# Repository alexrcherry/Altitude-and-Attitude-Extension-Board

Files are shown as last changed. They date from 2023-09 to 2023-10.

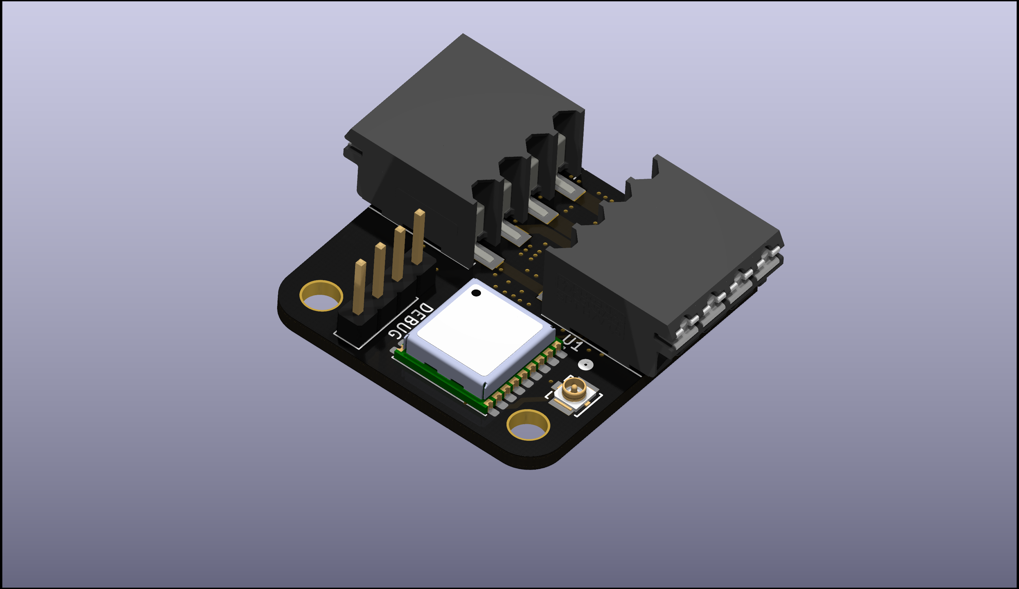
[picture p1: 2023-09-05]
AT&T/ATL_BACK.png

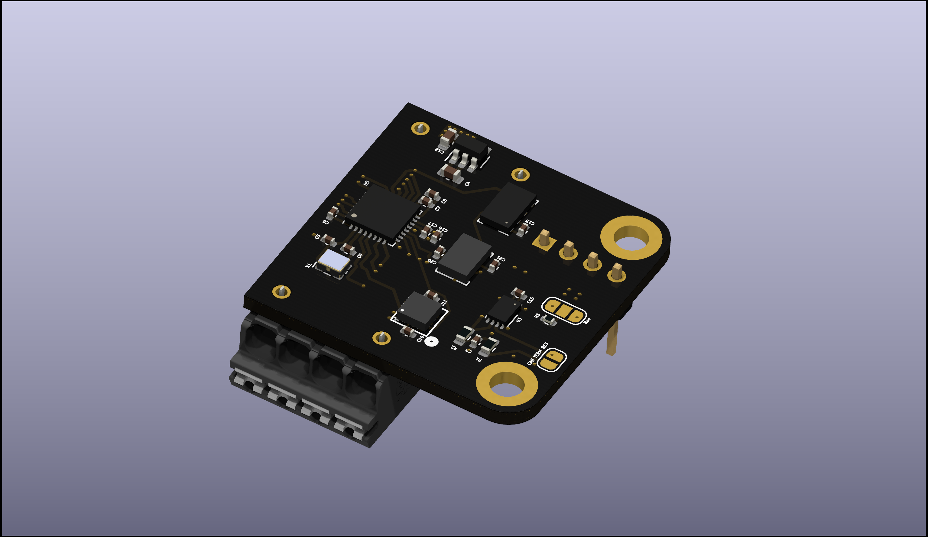
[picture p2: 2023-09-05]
AT&T/ATL_FRONT.png

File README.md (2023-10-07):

# Altitude-and-Attitude-Extension-Board
PCB design files for altitude and attitude extension board
## Purpose
The purpose of the Altitude and Attitude Extension Board is to measure the full state of a rocket. To do this, a gyroscope, accelerometer, gps, barometer and magnetometer are included on this board. A Kalman filter or some other means is necessary to get the full state of the rocket from the sensor data. The full state output of this board will be used to estimate the apogee of the rocket and to provide feedback for control systems.

| Requirement # | Requirement | Justification | Testing Plan |
| --- | --- | --- | --- |
| R-001 | Shall fit in 4” diameter body tube | PCB needs to fit into L1 kits & Olympus expected diameter. | Measure with calipers |
| R-002 | Will use 2x M2 or larger mounting bolts | Needs to be mounted easily inside the avionics bay. | X |
| R-003 | Will use 5v input power supply | The main power bus running the length of the rocket is 5v. | X |
| R-004 | Will draw less than 1A | The device should not greatly affect the power bus for other devices. Current is limited so that voltage sag is minimized. | X |
| R-005 | Will have 2x CAN high connection | Needs two connections so the device can be daisy chained. | X |
| R-006 | Will have 2x CAN low connections  | Needs two connections so the device can be daisy chained. | X |
| R-007 | Will have 2x Gnd connections | Needs two connections so the device can be daisy chained. | X |
| R-008 | Will have 2x 5v+ connections | Needs two connections so the device can be daisy chained. | X |
| R-009 | Will fulfill the requirements across the temperature range of -90 to 50 deg C | Needs to work in the sun on the launch pad and in the cold upper atmosphere. | Real conditions, freezer, oven? |
| R-010 | Will use CAN 2.0 | Communication needs to be compatible with all other boards, can 2.0 chosen for high speed. | X |
| R-011 | Should use STM32 microcontroller | This requirement is somewhat flexible, stm32 is greatly preferred because that is what the club currently has experience with. | X |
| R-012 | Should have greater than 1 deg heading accuracy over flight time | This information may be used for active control and needs to be as accurate as possible to minimize rocket dispersion. | |
| R-013 | Should be able to measure 10 g or greater acceleration | Testing will be done on solid rockets which generally have greater acceleration. | |
| R-014 | Should be able to measure altitude within < 5% error to 130km | Needs to measure altitude for a spaceshot. This may end up being done with radio ranging instead of IMU integration. | |
| R-015 | Should be able to detect launch, apogee, and landing | Software needs to send a signal to the main processing board for these important flight events so that logging rate can be modified. | |

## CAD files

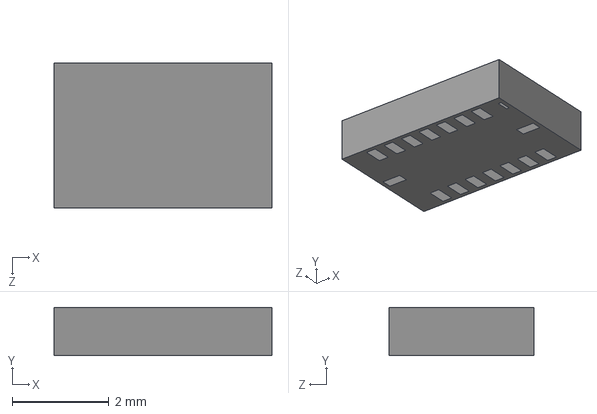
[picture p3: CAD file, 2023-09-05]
AT&T/Imported Symbols and Footprints/BMI088/KiCADv6/BMI088--3DModel-STEP-56544.STEP
4.50 x 1.00 x 3.00 mm

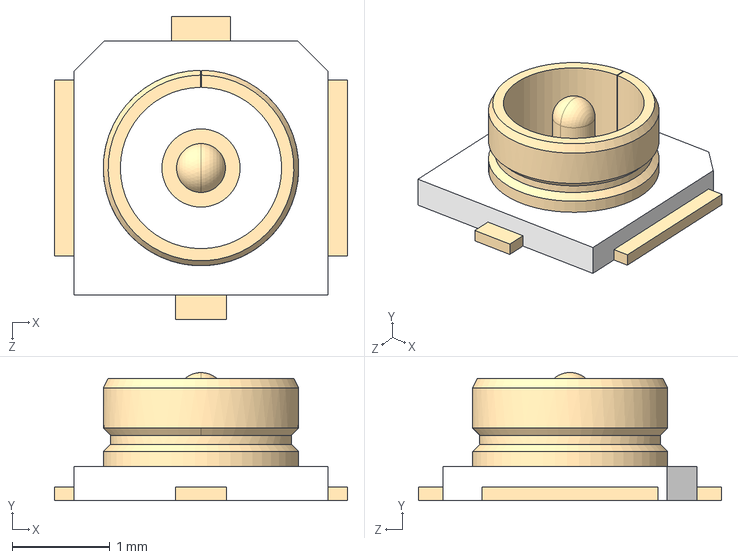
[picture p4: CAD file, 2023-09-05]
AT&T/Imported Symbols and Footprints/CONMHF1-SMD-G-T/CONMHF1-SMD-G-T.step
3.00 x 1.31 x 3.10 mm

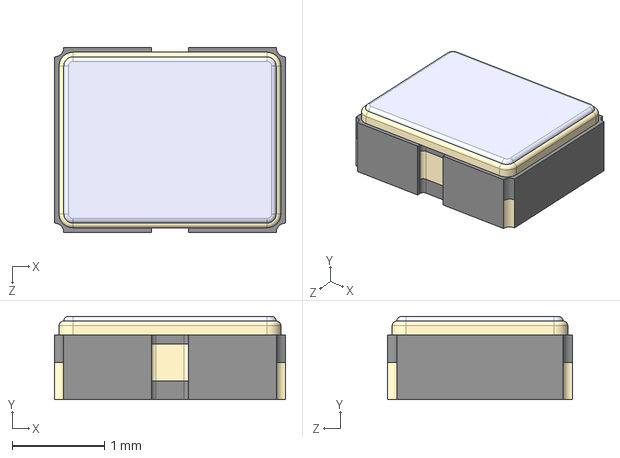
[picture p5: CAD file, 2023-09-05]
AT&T/Imported Symbols and Footprints/ECS-2520/ECS-2520MV-120-BN-TR.STEP
2.50 x 0.9 x 2.00 mm

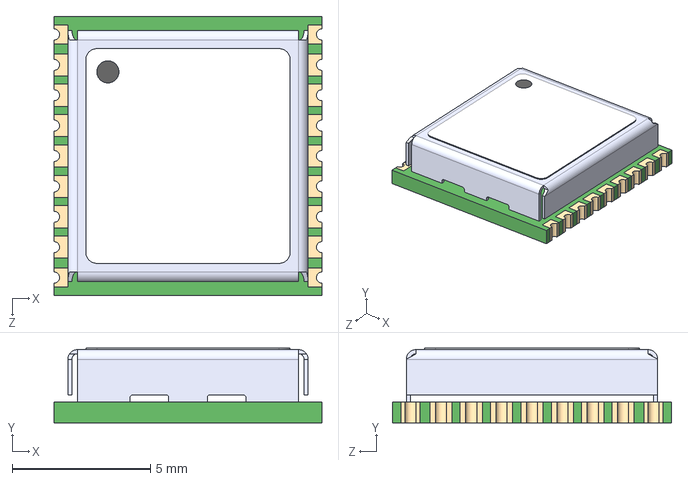
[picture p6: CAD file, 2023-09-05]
AT&T/Imported Symbols and Footprints/MAX-M10S/MAX-M8C-0-10--3DModel-STEP-56544.STEP
9.70 x 2.70 x 10.1 mm

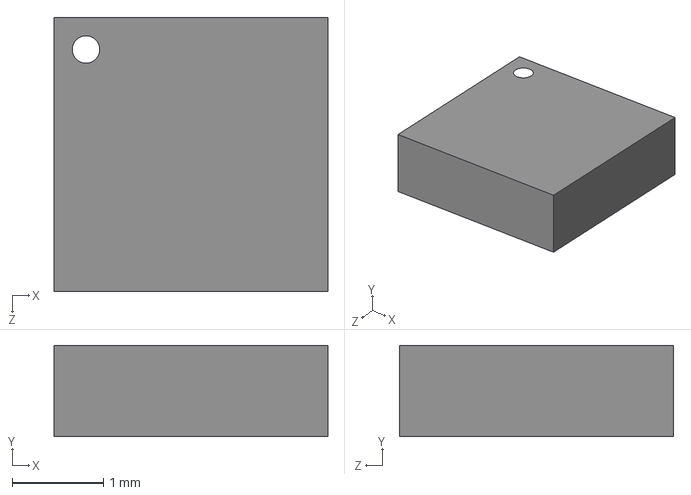
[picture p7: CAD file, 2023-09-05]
AT&T/Imported Symbols and Footprints/MMC5983MA/KiCADv6/MMC5983MA--3DModel-STEP-269445.STEP
3.00 x 1.00 x 3.00 mm

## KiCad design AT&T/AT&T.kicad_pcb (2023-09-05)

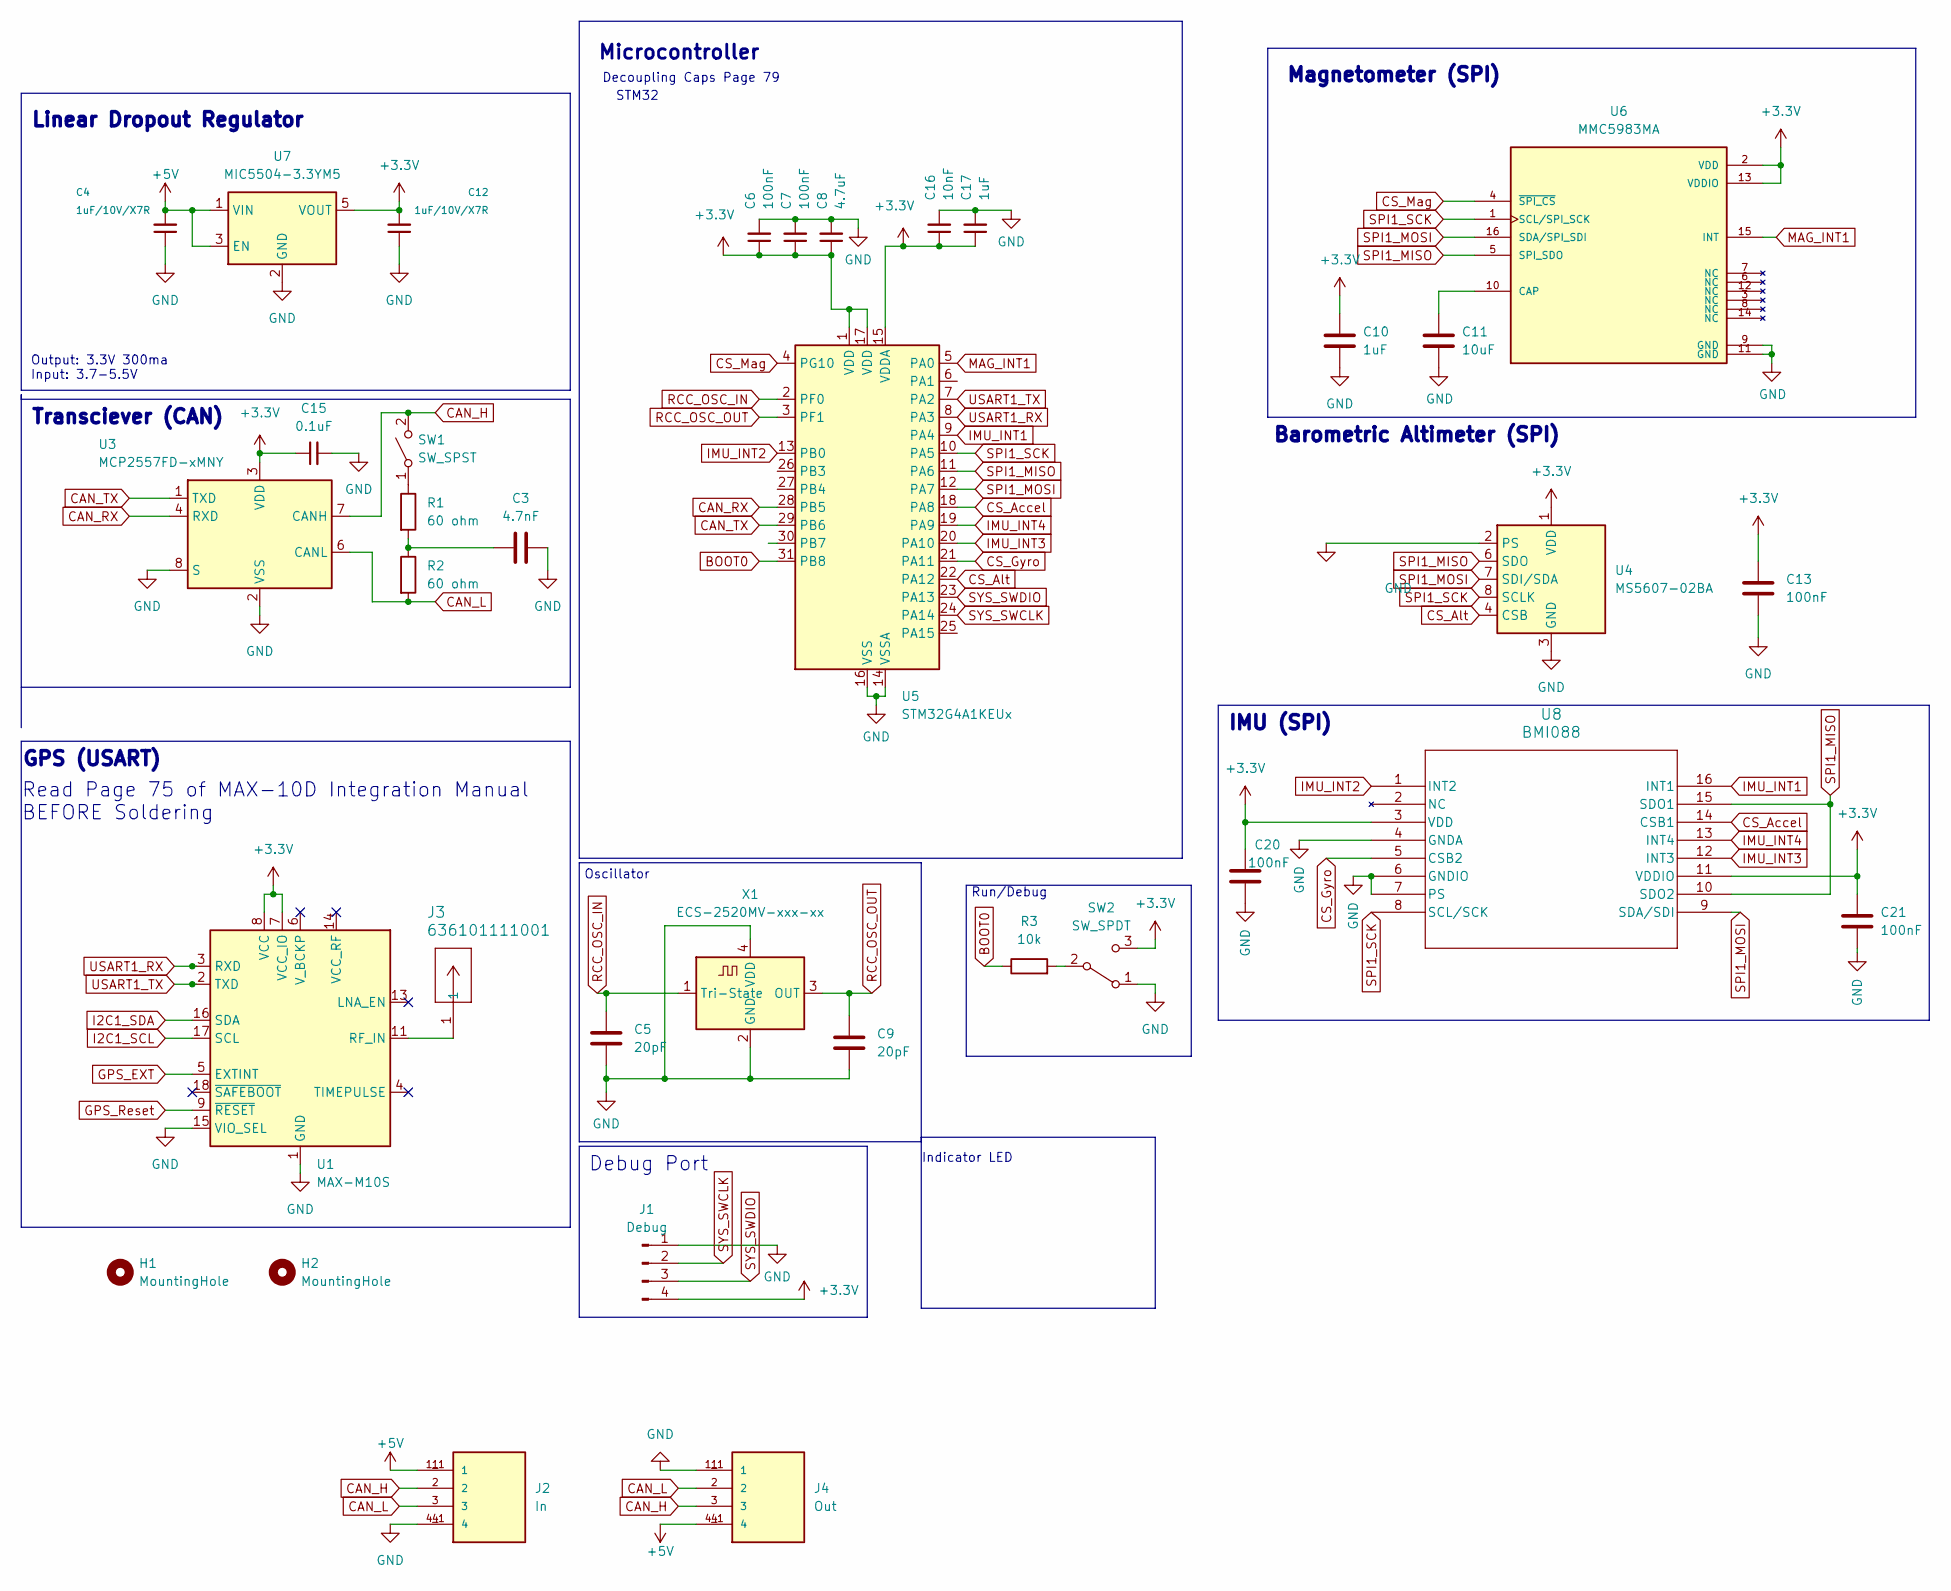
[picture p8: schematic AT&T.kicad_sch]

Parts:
C3: 4.7nF; C_0402_1005Metric
C4, C12: 1uF/10V/X7R; C_0603_1608Metric
C5, C9: 20pF; C_0402_1005Metric
C6, C7, C13, C20, C21: 100nF; C_0402_1005Metric
C8: 4.7uF; C_0402_1005Metric
C10, C17: 1uF; C_0402_1005Metric
C11: 10uF; C_0402_1005Metric
C15: 0.1uF; C_0402_1005Metric
C16: 10nF; C_0402_1005Metric
H1, H2: MountingHole; MountingHole_3.2mm_M3_DIN965_Pad_TopOnly
J1: Debug; PinHeader_1x04_P2.54mm_Vertical
J2: In; PHOENIX_1824543; PARTREV N/A; DigiKey_Part_Number 277-11572-2-ND
J3: 636101111001; CONN_636101111001_WRE
J4: Out; PHOENIX_1824543; PARTREV N/A; DigiKey_Part_Number 277-11572-2-ND
R1, R2: 60 ohm; R_0603_1608Metric
R3: 10k; R_0402_1005Metric
SW1: SW_SPST; SolderJumper-2_P1.3mm_Open_RoundedPad1.0x1.5mm
SW2: SW_SPDT; SolderJumper-3_P1.3mm_Open_RoundedPad1.0x1.5mm_NumberLabels
U1: MAX-M10S; ublox_MAX
U3: MCP2557FD-xMNY; TDFN-8-1EP_3x2mm_P0.5mm_EP1.80x1.65mm
U4: MS5607-02BA; LGA-8_3x5mm_P1.25mm
U5: STM32G4A1KEUx; QFN-32-1EP_5x5mm_P0.5mm_EP3.45x3.45mm
U6: MMC5983MA; MMC5983MA_MEM; PARTREV A
U7: MIC5504-3.3YM5; SOT-23-5
U8: BMI088; QFN_BMI085_BOS
X1: ECS-2520MV-xxx-xx; Oscillator_SMD_ECS_2520MV-xxx-xx-4Pin_2.5x2.0mm

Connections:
+3.3V: C6.1, C7.1, C8.1, C10.1, C12.2, C13.1, C15.1, C16.1, C17.1, C20.1, C21.1, J1.4, SW2.3 (C), U1.7 (VCC_IO), U1.8 (VCC), U3.3 (VDD), U4.1 (VDD), U5.1 (VDD), U5.15 (VDDA), U5.17 (VDD), U6.2 (VDD), U6.13 (VDDIO), U7.5 (VOUT), U8.3 (VDD), U8.11 (VDDIO); also elsewhere on the board
+5V: C4.2, J2.1, J2.1_1 (1), J4.4, J4.4_1 (4), U7.1 (VIN), U7.3 (EN)
BOOT0: R3.1, U5.31 (PB8)
CAN_H: J2.2, J4.3, SW1.2 (B), U3.7 (CANH); also elsewhere on the board
CAN_L: J2.3, J4.2, R2.2, U3.6 (CANL)
CAN_RX: U3.4 (RXD), U5.28 (PB5)
CAN_TX: U3.1 (TXD), U5.29 (PB6)
CS_Accel: U5.18 (PA8), U8.14 (CSB1)
CS_Alt: U4.4 (CSB), U4.5 (CSB), U5.22 (PA12)
CS_Gyro: U5.21 (PA11), U8.5 (CSB2)
CS_Mag: U5.4 (PG10), U6.4 (~SPI_CS)
GND: C3.2, C4.1, C5.2, C6.2, C7.2, C8.2, C9.2, C10.2, C11.2, C12.1, C13.2, C15.2, C16.2, C17.2, C20.2, C21.2, J1.1, J2.4, J2.4_1 (4), J4.1, J4.1_1 (1), SW2.1 (A), U1.1 (GND), U1.10 (GND), U1.12 (GND), U1.15 (VIO_SEL), U3.2 (VSS), U3.8 (S), U3.9 (VSS), U4.2 (PS), U4.3 (GND), U5.14 (VSSA), U5.16 (VSS), U5.32 (VSS), U5.33 (VSS), U6.9 (GND), U6.11 (GND), U7.2 (GND), U8.4 (GNDA), U8.6 (GNDIO), U8.7 (PS), X1.2 (GND), X1.4 (VDD); also elsewhere on the board
GPS_EXT: U1.5 (EXTINT)
GPS_Reset: U1.9 (~RESET)
I2C1_SCL: U1.17 (SCL)
I2C1_SDA: U1.16 (SDA)
IMU_INT1: U5.9 (PA4), U8.16 (INT1)
IMU_INT2: U5.13 (PB0), U8.1 (INT2)
IMU_INT3: U5.20 (PA10), U8.12 (INT3)
IMU_INT4: U5.19 (PA9), U8.13 (INT4)
MAG_INT1: U5.5 (PA0), U6.15 (INT)
unnamed: C3.1, R1.2, R2.1
unnamed 22: R1.1, SW1.1 (A); also elsewhere on the board
unnamed: R3.2, SW2.2 (B)
unnamed: J3.1, U1.11 (RF_IN)
unnamed: C11.1, U6.10 (CAP)
RCC_OSC_IN: C5.1, U5.2 (PF0), X1.1 (Tri-State)
RCC_OSC_OUT: C9.1, U5.3 (PF1), X1.3 (OUT)
SPI1_MISO: U4.6 (SDO), U5.11 (PA6), U6.5 (SPI_SDO), U8.10 (SDO2), U8.15 (SDO1)
SPI1_MOSI: U4.7 (SDI/SDA), U5.12 (PA7), U6.16 (SDA/SPI_SDI), U8.9 (SDA/SDI)
SPI1_SCK: U4.8 (SCLK), U5.10 (PA5), U6.1 (SCL/SPI_SCK), U8.8 (SCL/SCK)
SYS_SWCLK: J1.2, U5.24 (PA14); also elsewhere on the board
SYS_SWDIO: J1.3, U5.23 (PA13); also elsewhere on the board
USART1_RX: U1.3 (RXD), U5.8 (PA3)
USART1_TX: U1.2 (TXD), U5.7 (PA2)

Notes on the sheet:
Microcontroller
Output: 3.3V 300ma Input: 3.7-5.5V
Read Page 75 of MAX-10D Integration Manual BEFORE Soldering
Magnetometer (SPI)
Linear Dropout Regulator
Debug Port
Indicator LED
Decoupling Caps Page 79
Oscillator
Run/Debug
GPS (USART)
Transciever (CAN)
STM32
Barometric Altimeter (SPI)
IMU (SPI)

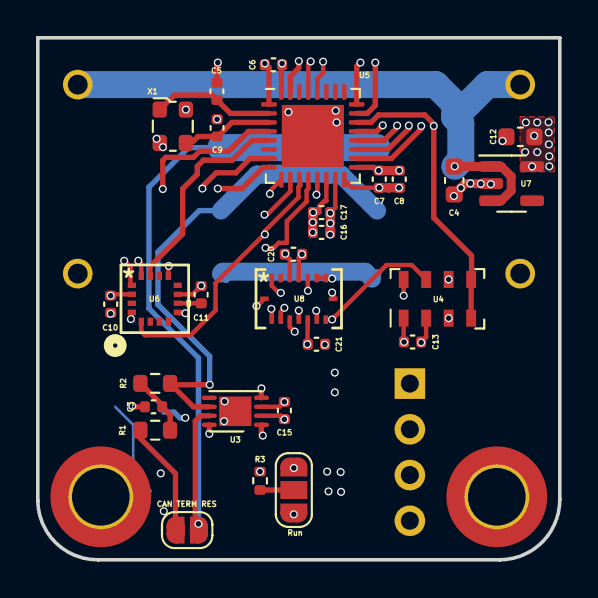
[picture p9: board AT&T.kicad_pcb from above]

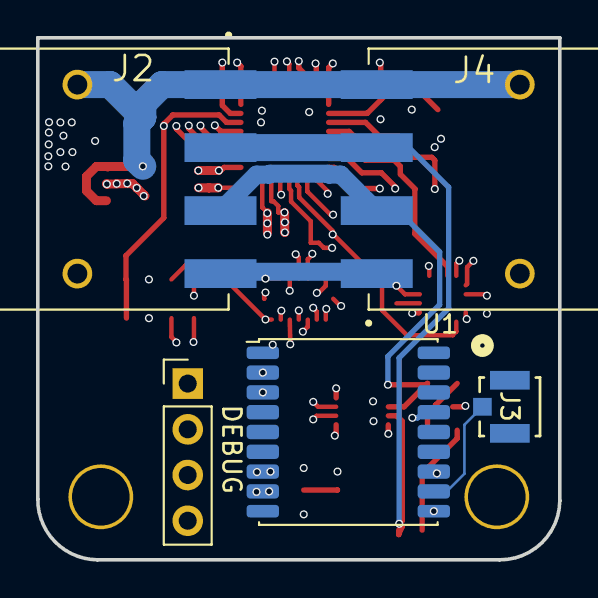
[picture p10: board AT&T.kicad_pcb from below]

Board: 6 copper layers, 29.0 x 29.0 mm, 35 parts (5 on the bottom side), 31 nets.

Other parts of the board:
CAN TERM RES: SW_SPST; SolderJumper-2_P1.3mm_Open_RoundedPad1.0x1.5mm
DEBUG: Debug; PinHeader_1x04_P2.54mm_Vertical

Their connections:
+3.3V: DEBUG.4; also elsewhere on the board
CAN_H: CAN TERM RES.2 (B); also elsewhere on the board
GND: DEBUG.1; also elsewhere on the board
unnamed 22: CAN TERM RES.1 (A); also elsewhere on the board
SYS_SWCLK: DEBUG.2; also elsewhere on the board
SYS_SWDIO: DEBUG.3; also elsewhere on the board
